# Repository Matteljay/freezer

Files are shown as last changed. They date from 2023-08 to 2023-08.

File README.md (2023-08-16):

# Freezer Fridge

- License: MIT License
- Author: Matteljay
- Language: Arduino C++
- IDE: Arduino.cc
- Homepage: https://libersystems.com

## Table of contents

- [About](#about)
- [Prototyping](#prototyping)
- [Physical PCB](#physical-pcb)
- [Schematic](#schematic)
- [Components](#components)
- [Safety Features](#safety-features)
  - [Hardware](#hardware)
  - [Software](#software)
- [Temperature Calibration](#temperature-calibration)
- [Formulas](#formulas)
  - [Straight Line](#straight-line)
  - [Exponential Moving Average](#exponential-moving-average)
- [Contact & Donate](CONTACT.md)

## About

Replacing the PCB of a malfunctioning [Miele](https://miele.com) freezer and
adding a temperature adjustment from 10°C to -22°C so it can work as a fridge
as well. How hard can it be? Well to do it somewhat safely, there are some
challenges. You can find my attempt here with detailed explanation of the
electronics components, formulas and the microcontroller [source
code](freezer-fridge.ino) packed with safety features. What you cannot find
here is any kind of guarantee that this project won't end up burning down your
house. This information is meant for educational purposes only. Use any of this
information at your own risk. [Donate](CONTACT.md) a coffee if you find any
useful information here.

## Prototyping

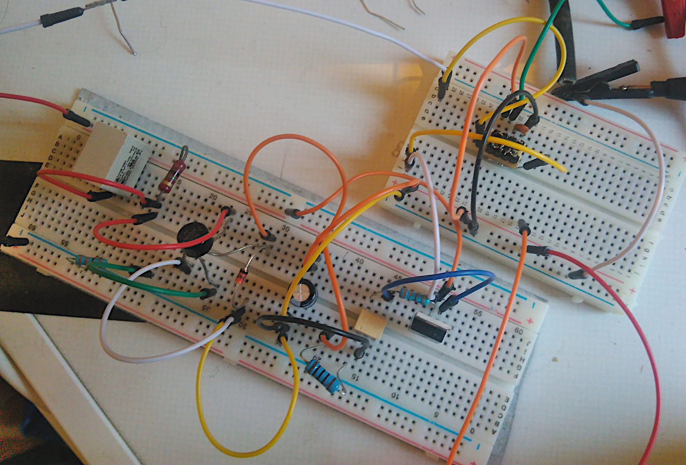
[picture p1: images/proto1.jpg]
Prototype


Both the prototype and the first version used a capacitive dropper circuit to
convert 230V AC to 5V DC. A 5V USB power plug was later disassembled for the
low profile isolated PCB inside to power the integrated circuits on the main
board. More prototype pictures are in the [images](images/) folder.

## Physical PCB

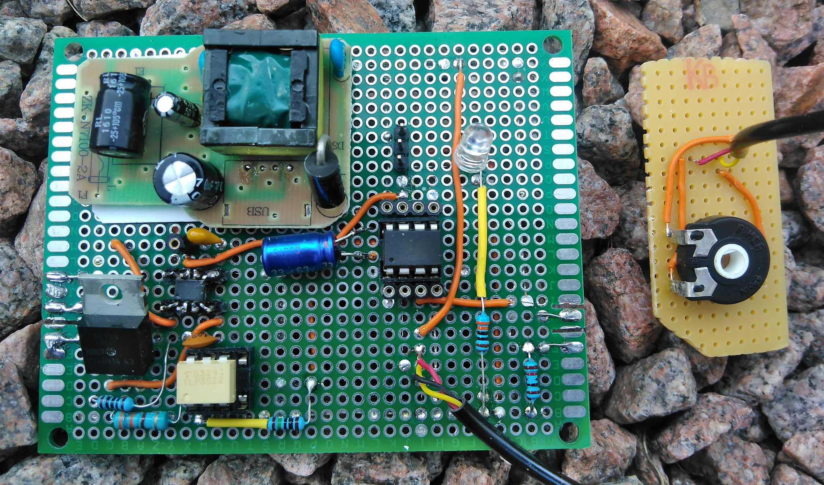
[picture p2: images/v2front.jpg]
PCB v2 front


Notice the horizontal cuts on the left and right sides of the board. This was
done with a fine metal saw so that external freezer hardware plugs can be
inserted: power, pump and temperature sensor. More screenshots and versions are
present in the [images](images/) folder.

The microcontroller is surrounded by female breakout pins which can be
connected wire for wire to an USBasp programmer. The three vertical male header
pins are connected to VCC, PIN 5 (LED) and GND for TTY console debug output.
That way, a PL2303 UART serial USB device can read all the messages from the
running Arduino.

## Schematic

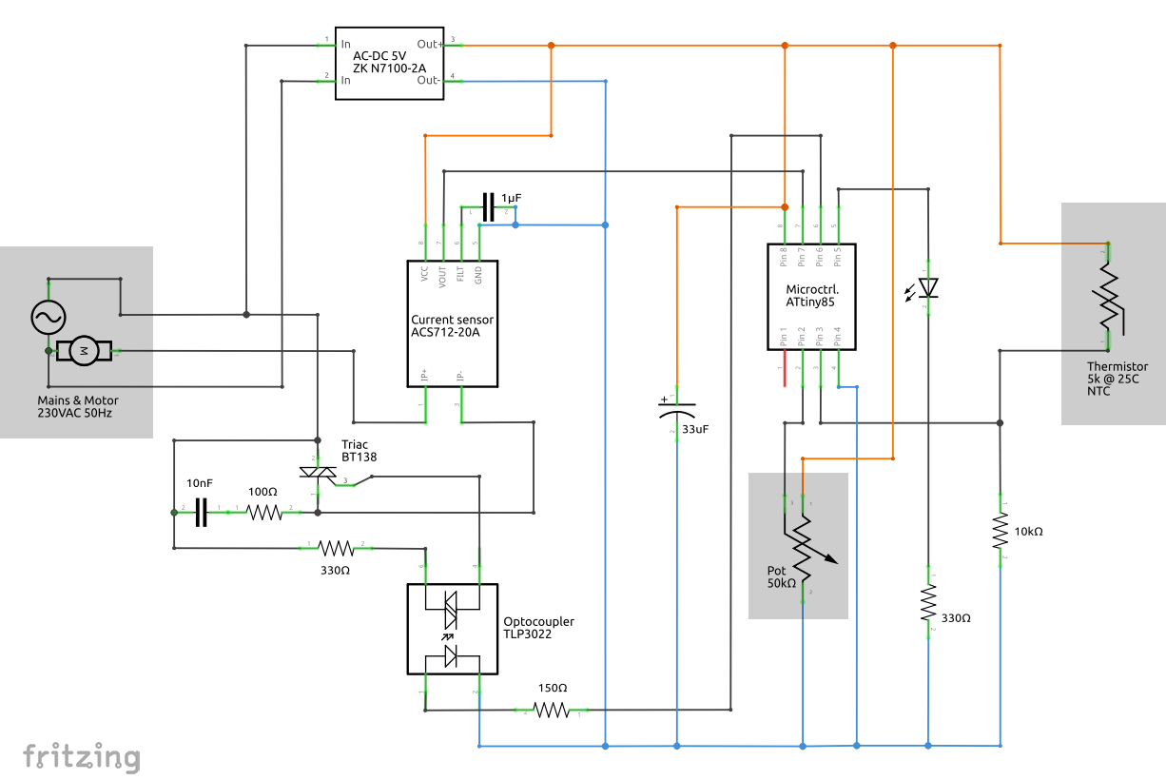
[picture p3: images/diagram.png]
PCB Schematic


The component placement and wiring on this schematic can roughly be translated
1:1 to the real physical layout. Concerning the shaded areas: the motor
(freezer pump) and thermistor are part of the freezer's unmodified hardware.
The potentiometer labeled *Pot* is a variable resistor used as the temperature
adjustment knob.

## Components

- **N7100-2A** disassembled European USB power plug 230V AC to 5V DC with a 2A
maximum.
- **ACS712-20A** Hall effect current sensor that can measure up to 20A maximum.
- **BT138-800** Sensitive logic level triac
- **TLP3022** Optocoupler of type photo-triac
- **ATtiny85** Low-power AVR RISC-based microcontroller
- **Thermistor** NTC type temperature resistor 5kΩ at 25°C
- **Motor** Freezer pump drawing around 4A at 230V AC when enabled by the triac

## Safety features

### Hardware

- An electrolytic capacitor across the ATtiny85's supply (pins 8 and 4) has
  noticeable error reducing effects on the operation. Especially time is kept
  much more accurately. This can be seen from TTY console character errors and
  even blinking LED timing.
- The combination of a 100Ω resistor with a 10nF capacitor (RC snubber) in
  parallel across the triac output should avoid it staying in a conductive
  state in case of sudden microcontroller shutdown.
- Switched from a capacitive dropper circuit to an isolated 5V power circuit.
- A clear coating was applied to the PCB's back to fixate the contacts, helping
  to prevent short circuits.
- A check was done to make sure the freezer is fused.

### Software

- *monitorAmps()* Use the ACS712 current sensor to determine if the pump is
  drawing normal and stable current. If not, do a detailed measurement cycle
  and watch for abnormal spikes.
- *pumpingTooLong()* Pumping for hours non-stop is not normal. If that
  happens, disable the pump completely and blink the LED forever with a one
  second interval.
- *badTempImpact()* After pumping non-stop for one hour, temperature **must**
  drop by at least 2°C. Otherwise the freezer's door is probably
  open. The pump is disabled completely and the LED blinks forever three times
  per second. Reconnect the power cable to restart the system.
- *fixTimeOverflows()* Arduino keeps time in *unsigned long* variable which
  can overflow (snap back to zero) after counting milliseconds for
  approximately 50 days. That means all values in the past must be manually
  reset as well.
- *checkTempSensor()* It temperature drops below -30°C, pause pump operation
  for a long time and notify with a non blinking LED.

## Temperature calibration

The temperature sensor is an NTC thermistor. This is a resistor component with
a *negative temperature coefficient* which means that the resistance decreases
with increasing temperature. Here are the measured values as the freezer pump
was started up from room temperature. Column A has the displayed value in
degrees Celsius from a simple plastic thermometer inside the middle freezer
drawer. Column B the pin value from the ATtiny. Column C is the resistance in
Ohms of the thermistor, manually measured with a multimeter.

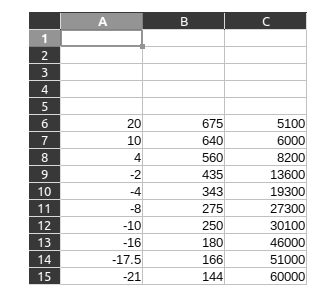
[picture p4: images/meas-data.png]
Measured points


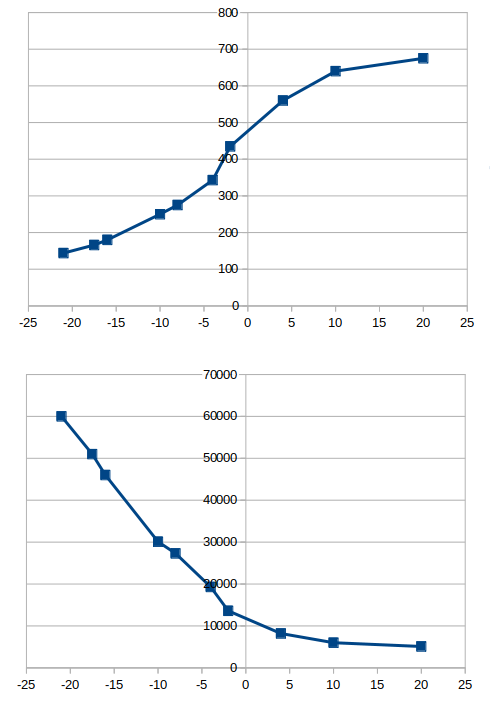
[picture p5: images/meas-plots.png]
Measured plots


The coldest areas inside the freezer are not located at the location of the
temperature sensor. It takes a couple of minutes for the temperature to become
uniform inside the freezer and be correctly sensed. The data above were
measurements taken as the pump was running so without this important
dissipation delay. However the shape of the graph is relevant in order to
decide how to relate measurements to real temperatures. Only the first graph is
relevant since only pin values will be measured by the microcontroller. An
approximation with a straight line will be used below. Judge for yourself if
this is accurate enough or you want to code a different math curve. Or perhaps
go for a multi line approach.

## Formulas

### Straight line

Pin values must be related to real temperatures somehow. As discussed above, a
simple straight line relation is chosen here. How to determine other points on
that line from having only two chosen points? This formula was used:

y - y1 = (y2 - y1) / (x2 - x1) * (x - x1)

Refactoring in a more useful format where **m** is the slope and **q** the
intercept on the y-axis:

y = m * x + q

m = (y2 - y1) / (x2 – x1)

q = y1 – m * x1

The comments in function [*calcVARs()*](freezer-fridge.ino) show the two
measured points that were really used to construct the final formula with
numerical values. To calculate the coefficients more easily, a
[LibreOffice](https://www.libreoffice.org/) Calc sheet is included
[here](line-2points.ods).

### Exponential moving average

The signals for temperature and the adjustment knob have some fluctuating noise
on their measurements. To account for that, initially the plan was to average
out those values with an SMA (simple moving average). However, using the EMA is
a better choice as it takes up less memory on the ATtiny since no arrays are
needed:

n = (m - p) * k + p

Here, **n** is the new EMA value, **m** is the measurement, **p** the previous
EMA and **k** the constant weighting of previous values, usually between 0 - 1.
The first term of that sum can become a floating point number, this format
was chosen to prevent that and work better with integer data types only:

n = (m + (1/k - 1) * p) / 1/k

Have a look at function [*calcVARs()*](freezer-fridge.ino) to see how much this
formula simplifies.

## Contact & Donate

More info here: [Contact](CONTACT.md)

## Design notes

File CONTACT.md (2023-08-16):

# Contact Info

- Author: Matteljay
- E-mail: matteljay-at-pm-dot-me

Donate if you find this app useful, fun, educational or you like to motivate
more projects like this. Donating allows me to allocate more of my time to this
type of open source coding.

## Cryptocurrency

    BTC:  14VZcizduTvUTesw4T9yAHZ7GjDDmXZmVs
    XMR:  4B6YQvbL9jqY3r1cD3ZvrDgGrRpKvifuLVb5cQnYZtapWUNovde7K5rc1LVGw3HhmTiijX21zHKSqjQtwxesBEe6FhufRGS
    ETH:  0x7C64707BD877f9cFBf0B304baf200cB1BB197354
    BCH:  qqvakvuwut8569w5q6w25kv72acf8299cun85v0l0z
    LTC:  ltc1q0whcrgdcljt4n34l58y5y3k4pj7dq7fqmw2srl
    DASH: XnMLmmisNAyDMT3Sr1rhpfAPfkMjDyUiwJ
    NANO: nano_3yztgrd4exg16r6dwxwc64fasdipi81aoe8yindsin7o31trqsgqanfi9fym
    LTO:  3JsaBxroCFW6xQzkeq38bRAjhwgsjr8ZegE
    BNB:  bnb1qvzenk3w9sfj5mgtqwsg0ph5m2x9m27x4krkgn
    BSC:  0x42DFc3B1c4f9f60c02846510Bd7e73a3aA22B376
    SCRT: secret1z2nv32clzqzz98ycqwmplfg5cu50ud9rhjj2gx

## Crypto fees

If you don't like high transaction fees, I recommend using a low fee chain like
SCRT or one of Ethereum's Layer II solutions such as
[Optimism](https://www.optimism.io/), [Arbitrum](https://arbitrum.io/) or
[Polygon](https://polygon.technology/).

## Scan with smartphone

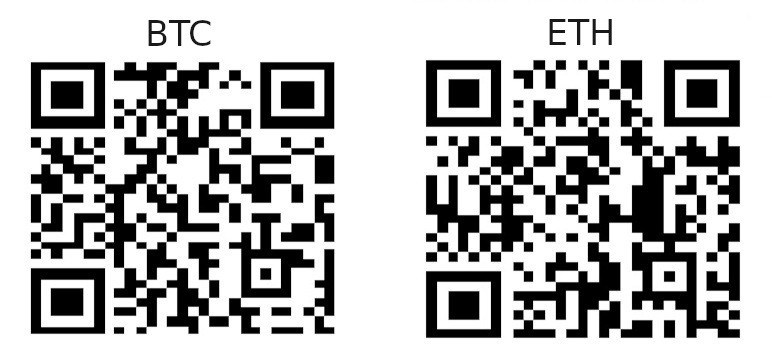
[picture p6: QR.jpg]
QR-codes


## Other methods

Please contact me for other payment channels.

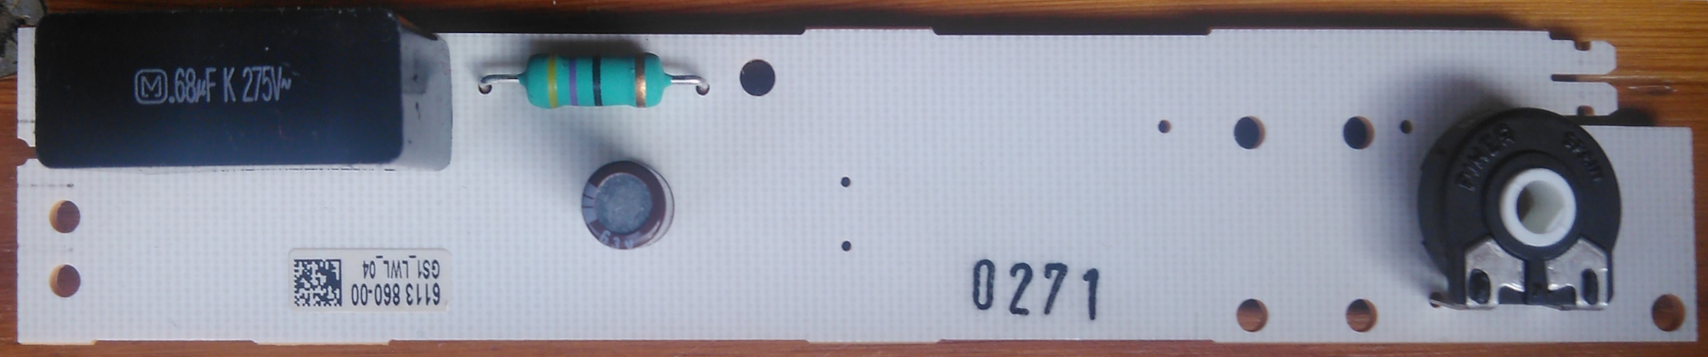
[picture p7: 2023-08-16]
images/original2.jpg

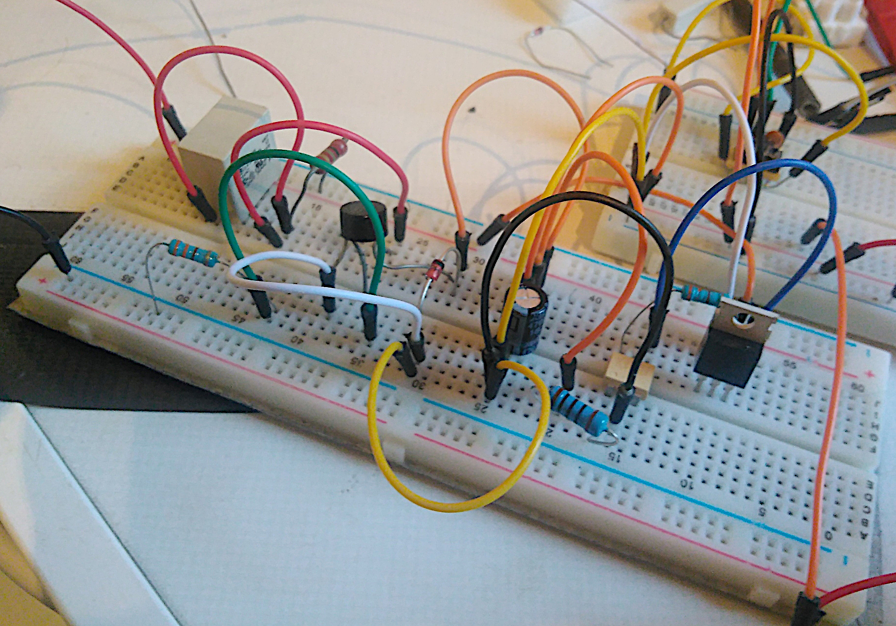
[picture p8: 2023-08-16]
images/proto2.jpg

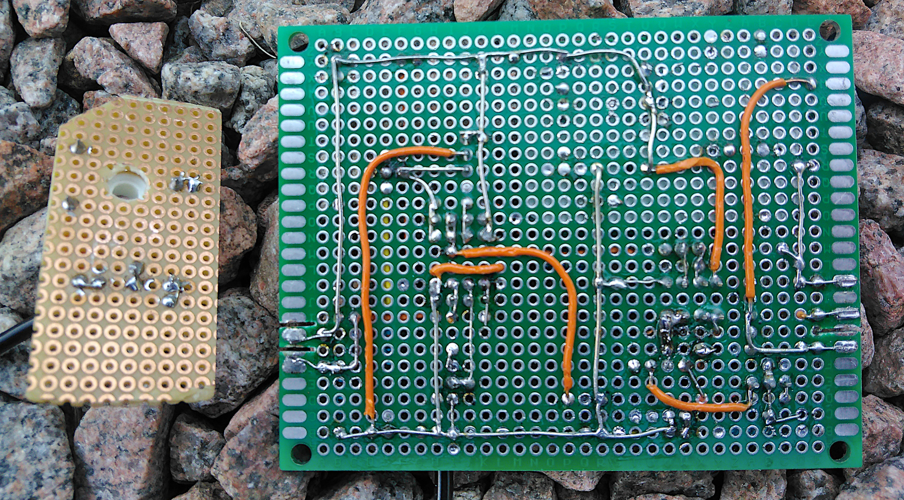
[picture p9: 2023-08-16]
images/v2back.jpg

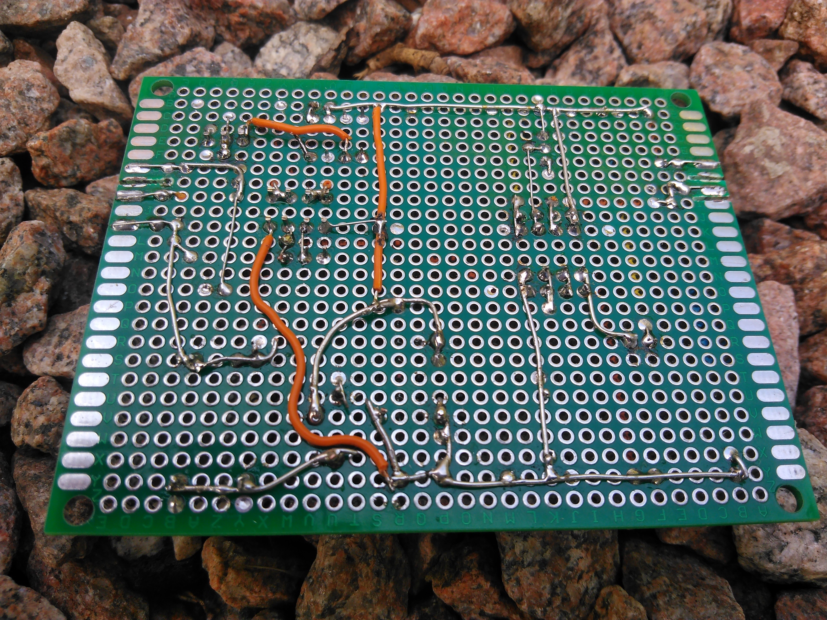
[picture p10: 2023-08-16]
images/v1back.jpg

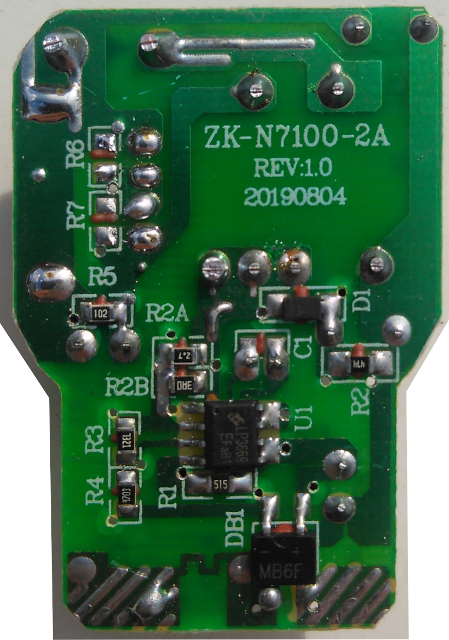
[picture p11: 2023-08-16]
images/ac-dc.jpg

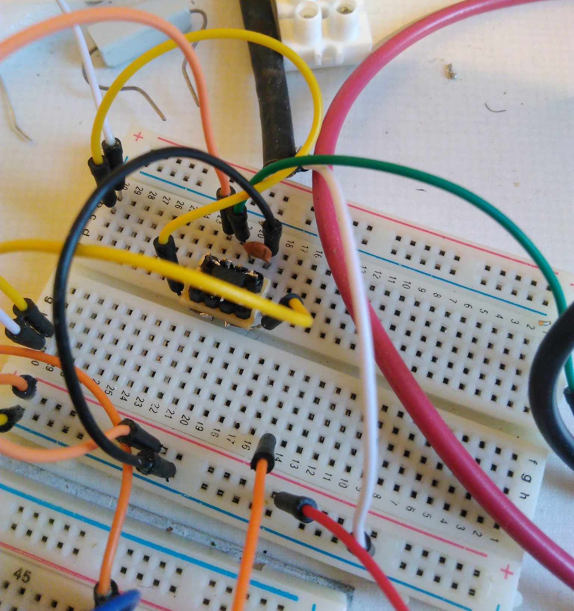
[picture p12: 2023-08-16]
images/proto4.jpg

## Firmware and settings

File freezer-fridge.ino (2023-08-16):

// Freezer - Fridge
//

#include <SoftwareSerial.h>

#define PIN_LED 0
#define PIN_COOL 1
#define PIN_AMPS A1
#define PIN_TSET A3
#define PIN_TEMP A2
#define PIN_NONE 255

//#define DEBUG
#define DEBUG_BOOT_DELAY_SEC 10
#define TOOCOLD_TEMP -30
#define TOOCOLD_ERROR_MINS 60
#define AMPS_EXPECTED 510 // in pin value
#define AMPS_BAD_SPIKE_RANGE 50 // in pin value
#define AMPS_BAD_ERROR_MINS 6
#define AMP_MEASURE_COUNT 20
#define PUMP_MAX_TIME_MINS 210
#define PUMP_MIN_RELAX_MINS 6
#define PUMP_MIN_RUN_MINS 8
#define IMPACT_TIME_MINS 60
#define IMPACT_TEMP_REQUIRED 2 // in Celsius
#define TEMP_HYSTERESIS 2 // in Celsius
#define LOOP_TIME_MS 2000

bool pumpRunning = false;
unsigned long pumpLastStartTime = 0;
unsigned long lastImpactTime = 0;
int lastImpactTemp = 0;
int pinTempEMA = 0;
int pinTsetEMA = 0;
int realTempEMA = 0;
int realTsetEMA = 0;

#ifdef DEBUG
  #define RX PIN_NONE
  #define TX PIN_LED
  SoftwareSerial mySerial(RX, TX);
  char msg[32];
  #define debugPrint(...) snprintf(msg, sizeof(msg), __VA_ARGS__); \
    msg[sizeof(msg) - 1] = '\0'; mySerial.println(msg);
#else
  #define debugPrint(...)
#endif

/* Varargs doesn't work (atm) with ATtiny85
void debugPrint(const char *fmt, ...) {
  #ifdef DEBUG
    char msg[40];
    va_list args;
    va_start(args, fmt);
    vsnprintf(msg, sizeof(msg), fmt, args);
    va_end(args);
    msg[sizeof(msg) - 1] = '\0';
    mySerial.println(msg);
  #endif
}
*/

void setup() {
  pinMode(PIN_COOL, OUTPUT);
  #ifdef DEBUG
    mySerial.begin(9600);
    delay(DEBUG_BOOT_DELAY_SEC * 1000);
    debugPrint("Hi");
  #else
    pinMode(PIN_LED, OUTPUT);
  #endif
  delay(500);
}

void loop() {
  fixTimeOverflows();
  calcVARs();
  checkTempSensor();
  stopRunningZone();
  monitorAmps();
  pumpingTooLong();
  badTempImpact(); // Leaking cold air, probably door open
  startRunningZone();
  delay(LOOP_TIME_MS);
}

void fixTimeOverflows() {
  const unsigned long now = millis();
  if(now < pumpLastStartTime) pumpLastStartTime = 0;
  if(now < lastImpactTime) lastImpactTime = 0;
}

void calcVARs() {
  // EMA - Exponential moving average formula
  // (m - p) * k + p <=> (m + (1/k - 1) * p) / 1/k
  // m: measurement, p: previousEMA, k: constant steepness/weighting
  // using k = 0.2 for easy use with integer type
  if(!pinTempEMA) {
    pinTempEMA = analogRead(PIN_TEMP);
  } else {
    pinTempEMA = (analogRead(PIN_TEMP) + 4 * pinTempEMA) / 5;
  }
  if(!pinTsetEMA) {
    pinTsetEMA = analogRead(PIN_TSET);
  } else {
    pinTsetEMA = (analogRead(PIN_TSET) + 4 * pinTsetEMA) / 5;
  }
  //debugPrint("calcVARs %d %d", pinTempEMA, pinTsetEMA);
  // Line from 2 points: y - y1 = (y2 - y1) / (x2 - x1) * (x - x1)
  // <=> y = m * x + q && m = (y2 - y1) / (x2 – x1) && q = y1 – m * x1
  // PIN_TEMP -> degC : 133 -> -27 (; 600 -> 8); 650 -> 16
  realTempEMA = pinTempEMA * 43 / 517 - 38;
  // PIN_TSET -> degC : 0 -> -20 ; 1024 -> 10
  realTsetEMA = pinTsetEMA * 30 / 1024 - 20;
  debugPrint("temps %d (%d) -> %d (%d)",
    realTempEMA, pinTempEMA, realTsetEMA, pinTsetEMA);
}

void checkTempSensor() {
  if(realTempEMA <= TOOCOLD_TEMP) {
    pumpSTOP();
    debugPrint("ERROR: TooCold STOP %d", realTempEMA);
    #ifdef DEBUG
      delay(PUMP_MIN_RELAX_MINS * 60000);
    #else
      digitalWrite(PIN_LED, HIGH);
      delay(TOOCOLD_ERROR_MINS * 60000);
      digitalWrite(PIN_LED, LOW);
    #endif
  }  
}

void monitorAmps() {
  if(!pumpRunning) return;
  const int amps = analogRead(PIN_AMPS);
  if(abs(amps - AMPS_EXPECTED) < AMPS_BAD_SPIKE_RANGE) return;
  //debugPrint("WARNING: One bad amp");
  int averageSpike = 0;
  const int pointDelay = 1000 / AMP_MEASURE_COUNT;
  for(int i = 0; i < AMP_MEASURE_COUNT; i++) {
    delay(pointDelay);
    averageSpike += abs(analogRead(PIN_AMPS) - AMPS_EXPECTED);
  }
  averageSpike /= AMP_MEASURE_COUNT;
  debugPrint("Spike %d", averageSpike);
  if(averageSpike < AMPS_BAD_SPIKE_RANGE) {
    return;
  }
  pumpSTOP();
  debugPrint("ERROR: Amps");
  #ifdef DEBUG
    delay(1 * 60000);
  #else
    digitalWrite(PIN_LED, HIGH);
    delay(AMPS_BAD_ERROR_MINS * 60000);
    digitalWrite(PIN_LED, LOW);
  #endif
}

void pumpingTooLong() {
  if(!pumpRunning) return;
  if(millis() - pumpLastStartTime <= PUMP_MAX_TIME_MINS * 60000) {
    return;
  }
  pumpSTOP();
  debugPrint("FATAL: Pumping %d", realTempEMA);
  #ifdef DEBUG
    while(true) { 
      delay(1000);
    }
  #else
    bool flashLED = true;
    while(true) {
      digitalWrite(PIN_LED, flashLED ? HIGH : LOW);
      flashLED = !flashLED;
      delay(1000);
    }
  #endif
}

void badTempImpact() {
  if(!pumpRunning) return;
  if(millis() - lastImpactTime < IMPACT_TIME_MINS * 60000) return;
  //const int tempNow = pinTEMPtoCelsius();
  if(lastImpactTemp - realTempEMA > IMPACT_TEMP_REQUIRED) {
    //debugPrint("Impact OK %d %d", lastImpactTemp, realTempEMA);
    lastImpactTime = millis();
    lastImpactTemp = realTempEMA;
    return;
  }
  pumpSTOP();
  debugPrint("FATAL: Impact");
  #ifdef DEBUG
    while(true) { 
      delay(1000);
    }
  #else
    bool flashLED = true;
    while(true) {
      digitalWrite(PIN_LED, flashLED ? HIGH : LOW);
      flashLED = !flashLED;
      delay(333);
    }
  #endif
}

/* Non blocking (more cumbersome) implementation
unsigned long pumpLastStopTime = 0;
if(pumpRelaxed())
bool pumpRelaxed() {
  if(pumpRunning) return false;
  if(millis() - pumpLastStopTime > PUMP_MIN_RELAX_MINS * 1000) {
    return true;
  }
  debugPrint("WARNING: Pump not relaxed");
  return false;
}
*/

void startRunningZone() {
  if(pumpRunning) return;
  if(realTempEMA > TOOCOLD_TEMP && realTempEMA >= realTsetEMA) {
    debugPrint("Zone START %d", realTsetEMA);
    pumpSTART();
  }
}

void stopRunningZone() {
  if(!pumpRunning) return;
  if(millis() - pumpLastStartTime < PUMP_MIN_RUN_MINS * 60000) return;
  const int targetTemp = realTsetEMA - abs(TEMP_HYSTERESIS);
  if(realTempEMA <= targetTemp) {
    pumpSTOP();
    debugPrint("Zone STOP %d", targetTemp);
    delay(PUMP_MIN_RELAX_MINS * 60000);
    debugPrint("Pump relaxed");
  }
}

void pumpSTART() {
  digitalWrite(PIN_COOL, HIGH);
  pumpRunning = true;
  pumpLastStartTime = millis();
  // "Impact" is the temp-delta monitored to see if the pump is having effect
  // Otherwise the door is probably open
  lastImpactTime = pumpLastStartTime;
  lastImpactTemp = realTempEMA;
  debugPrint("PUMP_START");
}

void pumpSTOP() {
  digitalWrite(PIN_COOL, LOW);
  pumpRunning = false;
  debugPrint("PUMP_STOP");
}

// EOF
